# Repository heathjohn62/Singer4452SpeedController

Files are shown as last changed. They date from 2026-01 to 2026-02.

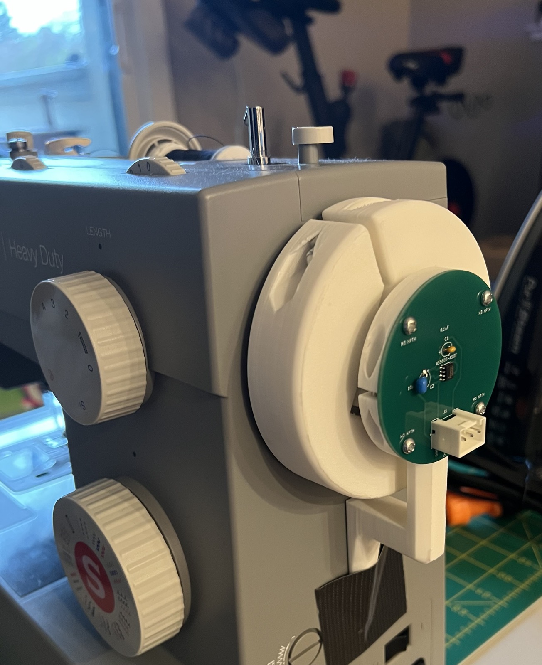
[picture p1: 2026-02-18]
images/rotary-encoder.jpg

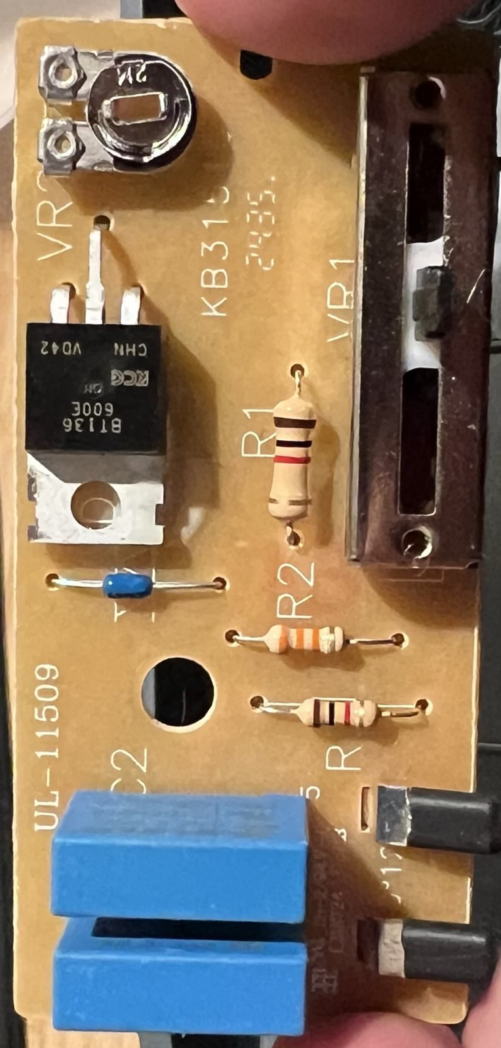
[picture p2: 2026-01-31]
foot-pedal-PCB/original-PCB-images/front.jpg

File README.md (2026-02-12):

# Singer4452-speed-controller

This project implements PID feedback to improve control over the Singer 4452 sewing machine. The modifications are non-destructive to the sewing machine. 

Implement this at your own risk. I do not have an electrical engineering degree nor am I a certified electrician. 120V AC flows through the sewing machine pedal and the PID regulator board, which can electrocute you, start fires, and break things. Don't perform work on circuits that are plugged into the wall. 

As an outline:
1. A rotary encoder tracks the position of the sewing needle by mounting externally to the knob on the side of the machine. The FreeCAD design for the rotary encoder is contained in "rotary-encoder-CAD". Some hardware, a magnet, rubber tape, duct tape, and a ball bearing are also required to assemble this. The PCB for the rotary encoder IC in contained in "speed-sensor-PCB."
2. A network of optoisolated resistors emulate the potentiometer in the existing pedal. Resistance is programmed by a MCU. The MCU and resistor network are enclosed in a chasis, and the design for the PCB is in the folder "Regulator-PCB." The STM32 was programmed in the STM32CubeIDE using the files in the folder "sewing-PID-STM32-program".
3. The circuit board in the original pedal is redesigned. The slide potentiometer provides input to the MCU instead of providing the timing to an RC oscillator as in the original pedal. The RC osillator is timed by the variable resistor network in the regulator PCB. The BT136-600E triac is exchanged for a higher current BT137-600E, and an additional 100 ohm and 0.1uF snubber is added to mitigate stress on the motor and triac. A fuse and varistor are added as short circuit and overvoltage protection. 

Errors and other notes:
- In my original rotary encoder design, pin 5 on the AS5600-ASOT was grounded. This was a mistake, and the pin should be left open. This is now fixed in KiCAD, but for my own sewing machine I just pried the IC pin off of the PCB. 
- The 5V barrel jack runs directly into the enclosure when positioned as it currently is on the PCB. I cut the barrel off and soldered the wires directly to the PCB. This is not currently fixed in the KiCAD design. 
- The AC mains connect to the foot pedal using 0.110" quick-connect tabs. I designed the board for two-prong 0.187" tabs (TE 1-726388-2), which don't fit the mains cables. I didn't want to pay for shipping again, so I bent one of the two prongs on the tabs so that one could be soldered into the PCB and the other into the mains cable. This is fine, but the better part to use would be something like TE 62395-1. 
- "foot-pedal-PCB" contains a folder "spice" with a (very approximate) simulation of the triac trigger circuit in the foot pedal. I used this to better understand the circuit in the original pedal and improve the design. In my hands, the triac model used by the simulation refuses to latch on PC, but works great on mac. 
- **This is likely not the best solution to this problem**. Using an optoisolated resistor network to adjust an RC timer takes up a ton of space and parts, and could be replaced by a circuit that exactly controls the phase angle modulation using only few optoisolators. I did not know I would be redesigning the foot pedal PCB after designing the regulator PCB. I'm now satisfied with the handling of my Singer 4452, so I have no plans to engineer this further. 
- Materials I ordered for this project can be found in the "orders" folder. Other things you would need include a soldering iron, hot air rework station or reflow oven, a drill, wire crimpers, STLink/V2 debugger and TAG-connect adapter, some metric machine screws and standoffs. I recommend anti-static precautions when working with STM32s.

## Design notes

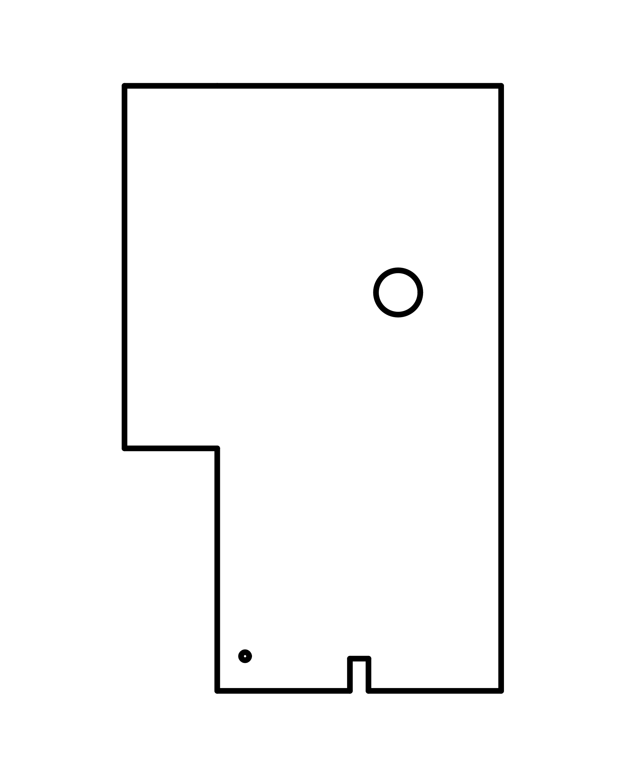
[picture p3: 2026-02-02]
foot-pedal-PCB/board-outline-CAD/board_outline-Page.png

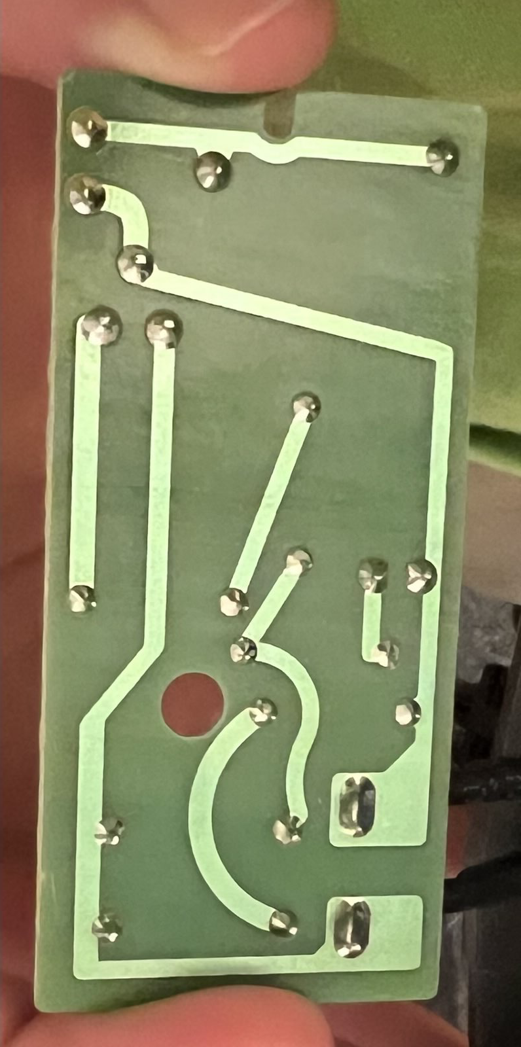
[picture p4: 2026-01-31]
foot-pedal-PCB/original-PCB-images/back.jpg

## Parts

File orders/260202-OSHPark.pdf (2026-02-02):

Invoice for | , generated 2026-02-02

Name
Email
Order ID

PCB : 260202-gerbers
Set Cost | $60.80 USD per set of 3
PCB Quantity | 3 (1 set of 3)
Project Subtotal | $60.80 USD

Shipping Information
Shipping Method | USPS Free Shipping
Shipping Cost | $0.00 USD
Shipping Address

Billing Information
Order date
Payment date
Payment method | Paypal
Payment status | Paid
Shipping Cost | $0.00 USD
Order Items | $60.80 USD
Total cost | $60.80 USD

OSH Park
311 B Ave
Suite B
Lake Oswego, OR 97034

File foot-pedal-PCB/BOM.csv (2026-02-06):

Reference | Qty | OrderQnty | Value | MFG | Mouser # | Description
C1,C2,C3 | 3 | 10 | 0.1uF | Vishay | 594-222233627104 | Safety Capacitors .1uF 10% 275volts
D1 | 1 | 2 | DB3 |  | 511-DB3 | 32V 2A Bidirectional trigger diode, DO-35
J1,J2 | 2 | 10 | 1-726388-2 | TE Connectivity | 571-1-726388-2 | Tab terminal,PCB, FASTON 187, straight TE Connectivity FASTON .187 Series , Straight Mount Angle PCB Tab Terminal, 4.75 x 0.81mm Tin Plated
Q1 | 1 | 2 | BT137-600E |  | 771-BT137-600E | Triacs RAIL TRIAC
R1 | 1 | 2 | 1k | Vishay | 71-CPF31K0000FKE14 | Metal Film Resistors - Through Hole 3watts 1Kohms 1% 100ppm
R2 | 1 | 2 | 22k | Vishay | 594-SFR25H0002202FA5 | Metal Film Resistors - Through Hole SFR25H 1% A5 22K
R3 | 1 | 2 | 1k |  | 594-SFR25H0001001FA5 | Metal Film Resistors SFR25H 1% A5 1K0
R4 | 1 | 2 | 100 | Vishay | 71-CPF3100R00FKE14 | Metal Film Resistors 3watts 100ohms 1% 100ppm
R5 | 1 | 2 | 200k | Vishay | 594-PR01000102003FA5 | Metal Film Resistors PR01 1% A5 200K
RV1 | 1 | 2 | 100k | Alpha (Taiwan) | 312-219BF-100K | Trimmer Resistors - Through Hole T7 YA 100K 20% BO e2
RV2 | 1 | 2 | 20k | Bourns | 652-3329H-1-203LF | Trimmer Resistors - Through Hole 1/4"RND 20KOHMS 10% 0.5WATTS

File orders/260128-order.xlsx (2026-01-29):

MFG # | Digikey # | Description | Qnty | MFG | Supplier | Notes | Link
SVH-21T-1.1 | 455-SVH-21T-1.1CT-ND | CONN SOCKET 18-22AWG CRIMP TIN | 30 | JST Sales America Inc. | Digikey | Solder wires directly onto the regulator PCB, use these external connectors to connect to pedal and rotary encoder.
B3P-VH-FB-B | 455-B3P-VH-FB-B-ND | CONN HEADER VERT 3POS 3.96MM | 10 | JST Sales America Inc. | Digikey
VHR-3N | 455-1184-ND | CONN RCPT HSG 3POS 3.96MM | 10 | JST Sales America Inc. | Digikey |  | https://www.digikey.com/en/products/detail/jst-sales-america-inc/VHR-3N/608625

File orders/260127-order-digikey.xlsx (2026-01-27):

Manufacturer Part # | Digikey Part # | Description | Qnty | MFG | Supplier | Notes | Link
AS5600-ASOT | AS5600-ASOTCT-ND | IC SENSOR MAG ROTARY 12BIT 8SOIC | 2 | ams-OSRAM USA Inc. | Digikey | Magnet rotary position sensor, 3.3V supply. | https://www.digikey.com/en/products/detail/ams-osram-usa-inc/AS5600-ASOT/4914338
STM32C092KCT6 | 497-STM32C092KCT6-ND | ARM® Cortex®-M0+ STM32C0 Microcontroller IC 32-Bit 48MHz 256KB (256K x 8) FLASH 32-LQFP (7x7) | 2 | STMicroelectronics | Digikey | Basic MCU | https://www.digikey.com/en/products/detail/stmicroelectronics/STM32C092KCT6/25935636
TRE06S050-A-01E03 VI | 2034-TRE06S050-A-01E03VI-ND | 5V 6 W AC/DC External Wall Mount (Class II) Adapter Fixed Blade Input | 1 | Cincon | Digilkey | Power Supply | https://www.digikey.com/en/products/detail/cincon-electronics-co-ltd/TRE06S050-A-01E03-VI/12168086
LP2985IM5X-3.3/NOPB | LP2985IM5X-3.3/NOPBCT-ND | Linear Voltage Regulator IC Positive Fixed 1 Output 150mA SOT-23-5 | 2 | TI | Digikey | LDO Regulator | https://www.digikey.com/en/products/detail/texas-instruments/LP2985IM5X-3-3-NOPB/367679
PJ-059A | CP-059A-ND | CONN PWR JACK 2X5.5MM SOLDER | 2 | Same Sky | Digikey | Power Connector | https://www.digikey.com/en/products/detail/same-sky-formerly-cui-devices/PJ-059A/1644607
LH1546AT | 751-LH1546AT-ND | Solid State Photo-Coupled Relay (Photorelay) SPST-NO (1 Form A) 6-DIP (0.300", 7.62mm) | 17 | Vishay | Digikey | SSR Relay ( I need 12) | https://www.digikey.com/en/products/detail/vishay-semiconductor-opto-division/LH1546AT/4072652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
LR1F680R | A105963CT-ND | 680 Ohms ±1% 0.6W Through Hole Resistor Axial Metal Film | 50 | TE Connectivity | Digikey | For LED current limit in SSR | https://www.digikey.com/en/products/detail/te-connectivity-passive-product/LR1F680R/2381276
2N3904 | 4878-2N3904CT-ND | Bipolar (BJT) Transistor NPN 40 V 200 mA 300MHz 625 mW Through Hole TO-92 | 20 | Diotec Semiconductor | Digikey | To drive LED in SSR (12) | https://www.digikey.com/en/products/detail/diotec-semiconductor/2N3904/13164701
RNF14FTD22R1 | RNF14FTD22R1CT-ND | 22.1 Ohms ±1% 0.25W, 1/4W Through Hole Resistor Axial Flame Retardant Coating, Safety Metal Film | 10 | Stackpole Electronics Inc | Digikey | Resistance Grid | https://www.digikey.com/en/products/detail/stackpole-electronics-inc/RNF14FTD22R1/1706712
MFR-25FRF52-44R2 | 13-MFR-25FRF52-44R2CT-ND | 44.2 Ohms ±1% 0.25W, 1/4W Through Hole Resistor Axial Metal Film | 10 | YAGEO | Digikey | Resistance Grid | https://www.digikey.com/en/products/detail/yageo/MFR-25FRF52-44R2/14761
MFR-25FBF52-88R7 | 88.7XBK-ND | 88.7 Ohms ±1% 0.25W, 1/4W Through Hole Resistor Axial Metal Film | 10 | YAGEO | Digikey | Resistance Grid | https://www.digikey.com/en/products/detail/yageo/MFR-25FBF52-88R7/12785
MFR-25FBF52-178R | 178XBK-ND | 178 Ohms ±1% 0.25W, 1/4W Through Hole Resistor Axial Metal Film | 10 | YAGEO | Digikey | Resistance Grid | https://www.digikey.com/en/products/detail/yageo/MFR-25FBF52-178R/12845
MFR-25FBF52-357R | 357XBK-ND | 357 Ohms ±1% 0.25W, 1/4W Through Hole Resistor Axial Metal Film | 10 | YAGEO | Digikey | Resistance Grid | https://www.digikey.com/en/products/detail/yageo/MFR-25FBF52-357R/12911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
MFR-25FBF52-715R | 715XBK-ND | 715 Ohms ±1% 0.25W, 1/4W Through Hole Resistor Axial Metal Film | 10 | YAGEO | Digikey | Resistance Grid | https://www.digikey.com/en/products/detail/yageo/MFR-25FBF52-715R/12983
MFR-25FBF52-1K43 | 13-MFR-25FBF52-1K43-ND | 1.43 kOhms ±1% 0.25W, 1/4W Through Hole Resistor Axial Metal Film | 10 | YAGEO | Digikey | Resistance Grid | https://www.digikey.com/en/products/detail/yageo/MFR-25FBF52-1K43/13042
MFR-25FBF52-2K87 | 2.87KXBK-ND | 2.87 kOhms ±1% 0.25W, 1/4W Through Hole Resistor Axial Metal Film | 10 | YAGEO | Digikey | Resistance Grid | https://www.digikey.com/en/products/detail/yageo/MFR-25FBF52-2K87/13116
MFR-25FRF52-5K76 | 13-MFR-25FRF52-5K76CT-ND | 5.76 kOhms ±1% 0.25W, 1/4W Through Hole Resistor Axial Metal Film | 10 | YAGEO | Digikey | Resistance Grid | https://www.digikey.com/en/products/detail/yageo/MFR-25FRF52-5K76/14962
MFR-25FBF52-11K5 | 11.5KXBK-ND | 11.5 kOhms ±1% 0.25W, 1/4W Through Hole Resistor Axial Metal Film | 10 | YAGEO | Digikey | Resistance Grid | https://www.digikey.com/en/products/detail/yageo/MFR-25FBF52-11K5/13230
MFR-25FBF52-23K2 | 23.2KXBK-ND | 23.2 kOhms ±1% 0.25W, 1/4W Through Hole Resistor Axial Metal Film | 10 | YAGEO | Digikey | Resistance Grid | https://www.digikey.com/en/products/detail/yageo/MFR-25FBF52-23K2/13288
MFR-25FRF52-46K4 | 13-MFR-25FRF52-46K4CT-ND | 46.4 kOhms ±1% 0.25W, 1/4W Through Hole Resistor Axial Metal Film | 10 | YAGEO | Digikey | Resistance Grid | https://www.digikey.com/en/products/detail/yageo/MFR-25FRF52-46K4/15046
MFR-25FBF52-93K1 | 93.1KXBK-ND | 93.1 kOhms ±1% 0.25W, 1/4W Through Hole Resistor Axial Metal Film | 10 | YAGEO | Digikey | Resistance Grid | https://www.digikey.com/en/products/detail/yageo/MFR-25FBF52-93K1/13467
STS232050UL40 | 283-STS232050UL40CT-ND | 15V Clamp 4A (8/20µs) Ipp Tvs Diode Surface Mount SOT-23 | 10 | Eaton - Electronics Division | Digikey | MCU protection | https://www.digikey.com/en/products/detail/eaton-electronics-division/STS232050UL40/13280445
1.5KE6.8CA | 13-1.5KE6.8CA/BCT-ND | TVS Diode for power supply (Bidirectional) | 2 | YAGEO | Digikey | MCU protection
1.5KE6.8A | 1.5KE6.8ALFCT-ND | TVS Diode for power 5V supply (Unidirectional) | 2 | Littelfuse Inc. | Digikey | MCU protection and reverse polarity protection. | https://www.digikey.com/en/products/detail/littelfuse-inc/1-5KE6-8A/285842
C320C104K5R5TA | 399-4264-ND | 0.1 µF ±10% 50V Ceramic Capacitor X7R Radial | 10 | Kemet | Digikey | Decoupling | https://www.digikey.com/en/products/detail/kemet/C320C104K5R5TA/818040
FG20X7R1H106KRT06 | 445-173297-1-ND | 10 µF ±10% 50V Ceramic Capacitor X7R Radial | 10 | TDK Corporation | Digikey | Power Supply Cap for AS5600 | https://www.digikey.com/en/products/detail/tdk-corporation/FG20X7R1H106KRT06/5811902
FG24X7R1E475KRT00 | 445-FG24X7R1E475KRT00-ND | 4.7 µF ±10% 25V Ceramic Capacitor X7R Radial | 10 | TDK Corporation | Digikey | Decoupling | https://www.digikey.com/en/products/detail/tdk-corporation/FG24X7R1E475KRT00/7326742
8019 | 469-1003-ND | Magnet Neodymium Iron Boron (NdFeB) N35 0.250" Dia x 0.250" H (6.35mm x 6.35mm) | 2 | Radial Magnets Inc. | Digikey | Strong magnet | https://www.digikey.com/en/products/detail/radial-magnets-inc/8019/555327
PDB181-K420K-203B | PDB181-K420K-203B-ND | 20k Ohm 1 Gang Linear Panel Mount Potentiometer 1.0 Turns Carbon 0.2W, 1/5W PC Pins | 3 | Bourns | Digikey | for foot pedal | https://www.digikey.com/en/products/detail/bourns-inc/PDB181-K420K-203B/2564752?gclsrc=aw.ds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
B32621A6103J189 | 495-B32621A6103J189CT-ND | 10000 pF Film Capacitor 400V 630V Polypropylene (PP), Metallized - Stacked Radial | 2 | EPCOS - TDK Electronics | Digikey | noise regulation power supply | https://www.digikey.com/en/products/detail/epcos-tdk-electronics/B32621A6103J189/3491369
MFR-25FRF52-10K | 13-MFR-25FRF52-10KCT-ND | 10 kOhms ±1% 0.25W, 1/4W Through Hole Resistor Axial Metal Film | 50 | YAGEO | Digikey | 2N904 Gate Resistor | https://www.digikey.com/en/products/detail/yageo/MFR-25FRF52-10K/14626

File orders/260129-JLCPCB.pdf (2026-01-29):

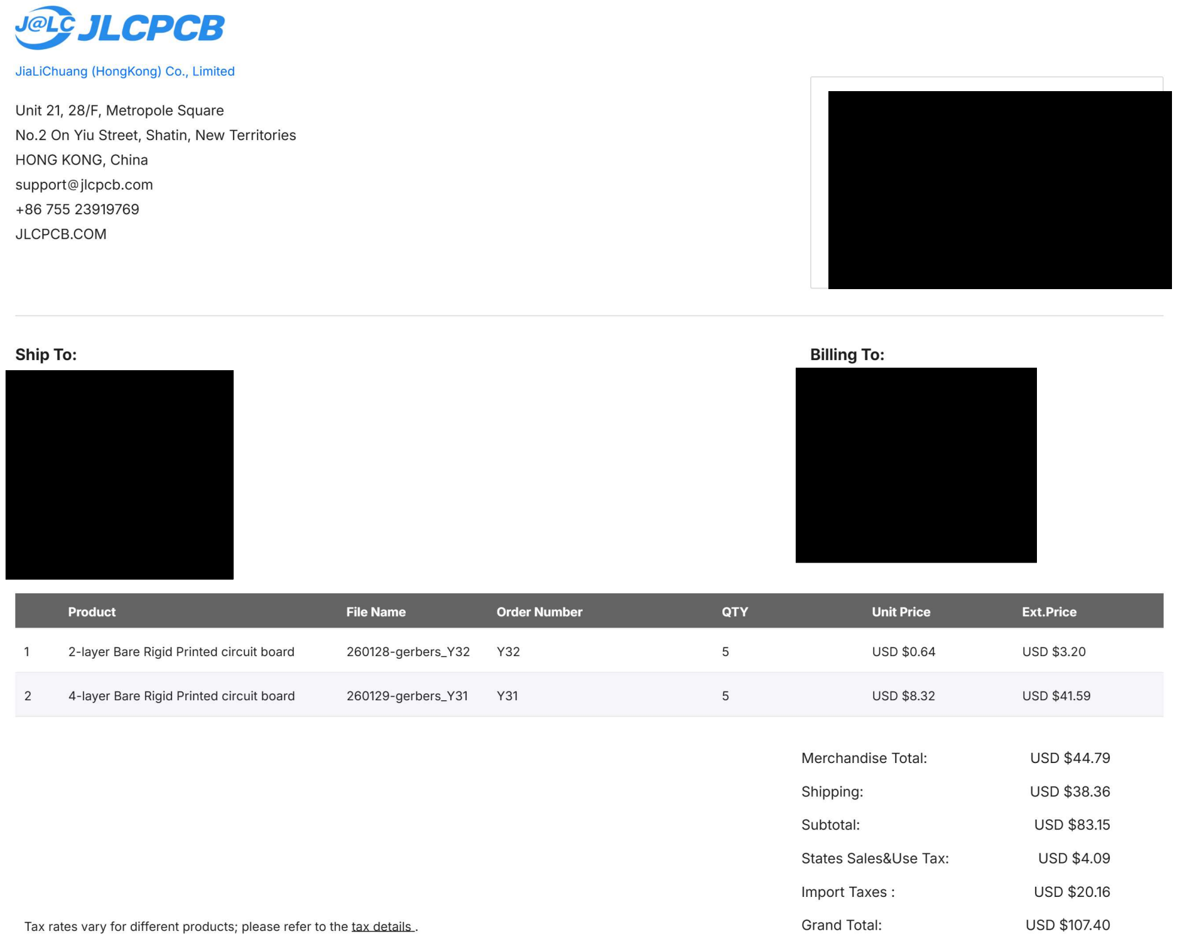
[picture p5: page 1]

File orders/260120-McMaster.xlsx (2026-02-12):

MFG # | Description | Price | Qnty | MFG | Notes | Link
5652N161 | Fabric-Reinforced Multipurpose Neoprene Strip with Adhesive-Back, High-Strength, 2" x 36", 1/16" Thick |  | 1 | Mcmaster Carr |  | https://www.mcmaster.com/5652N161/

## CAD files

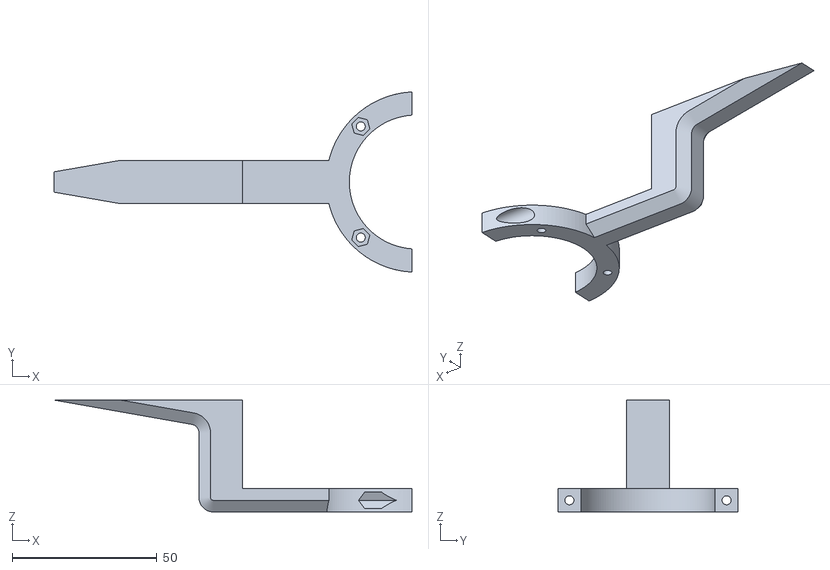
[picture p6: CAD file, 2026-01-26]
rotary-encoder-CAD/260126-lower-PCB-mount.stl
123.5 x 62.1 x 38.6

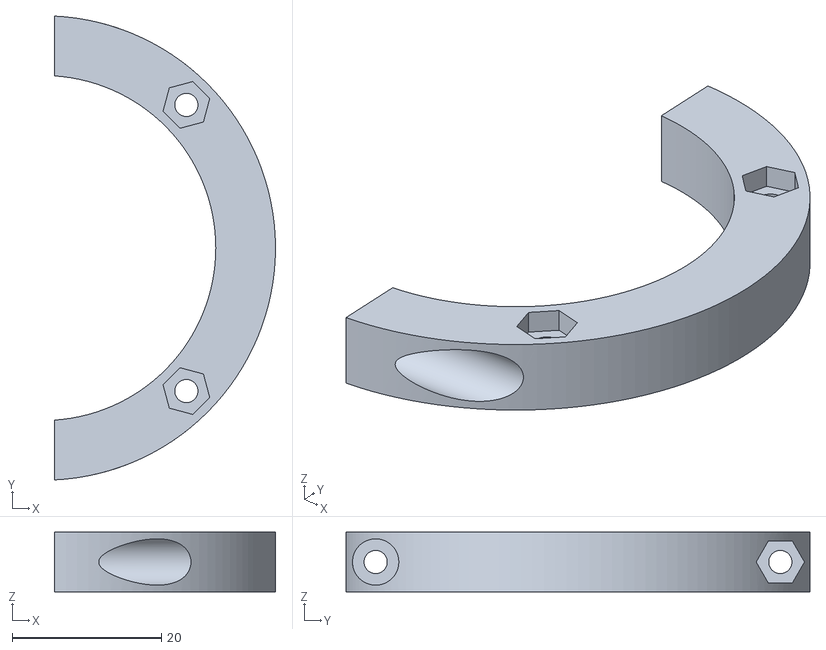
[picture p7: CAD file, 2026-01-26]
rotary-encoder-CAD/260126-upper-PCB-mount.stl
29.6 x 62.1 x 8.00

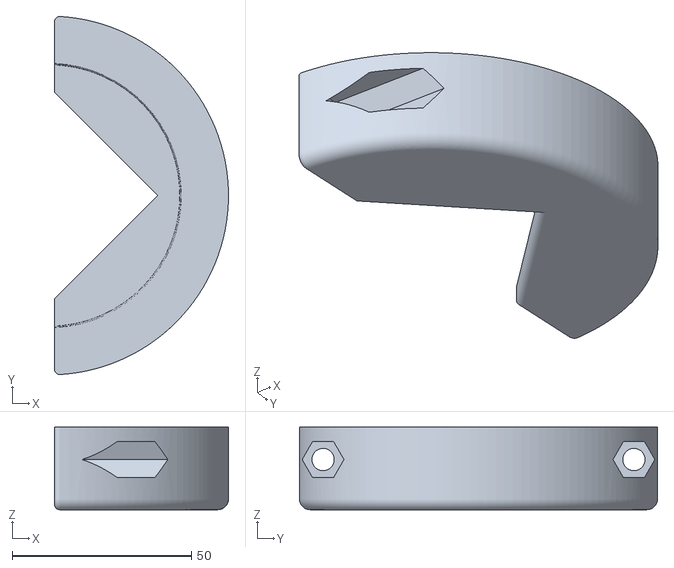
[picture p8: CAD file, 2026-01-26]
rotary-encoder-CAD/260125-upper-grip.stl
48.5 x 99.8 x 23.0

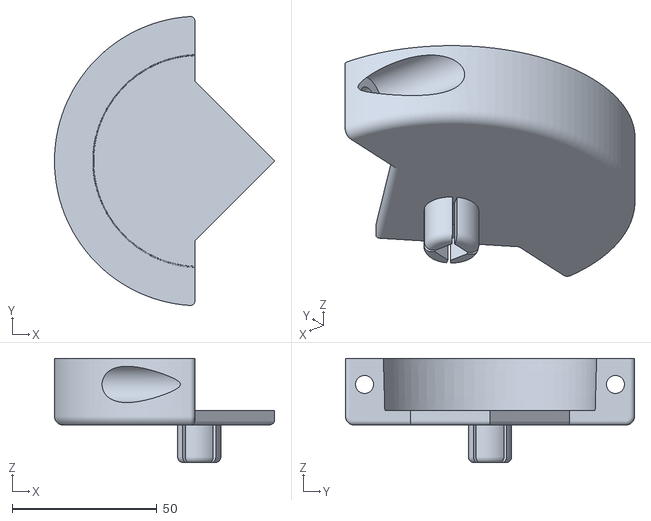
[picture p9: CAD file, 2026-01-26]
rotary-encoder-CAD/260125-lower-grip.stl
76.0 x 99.8 x 36.0

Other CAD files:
foot-pedal-PCB/board-outline-CAD/board_outline.FCStd

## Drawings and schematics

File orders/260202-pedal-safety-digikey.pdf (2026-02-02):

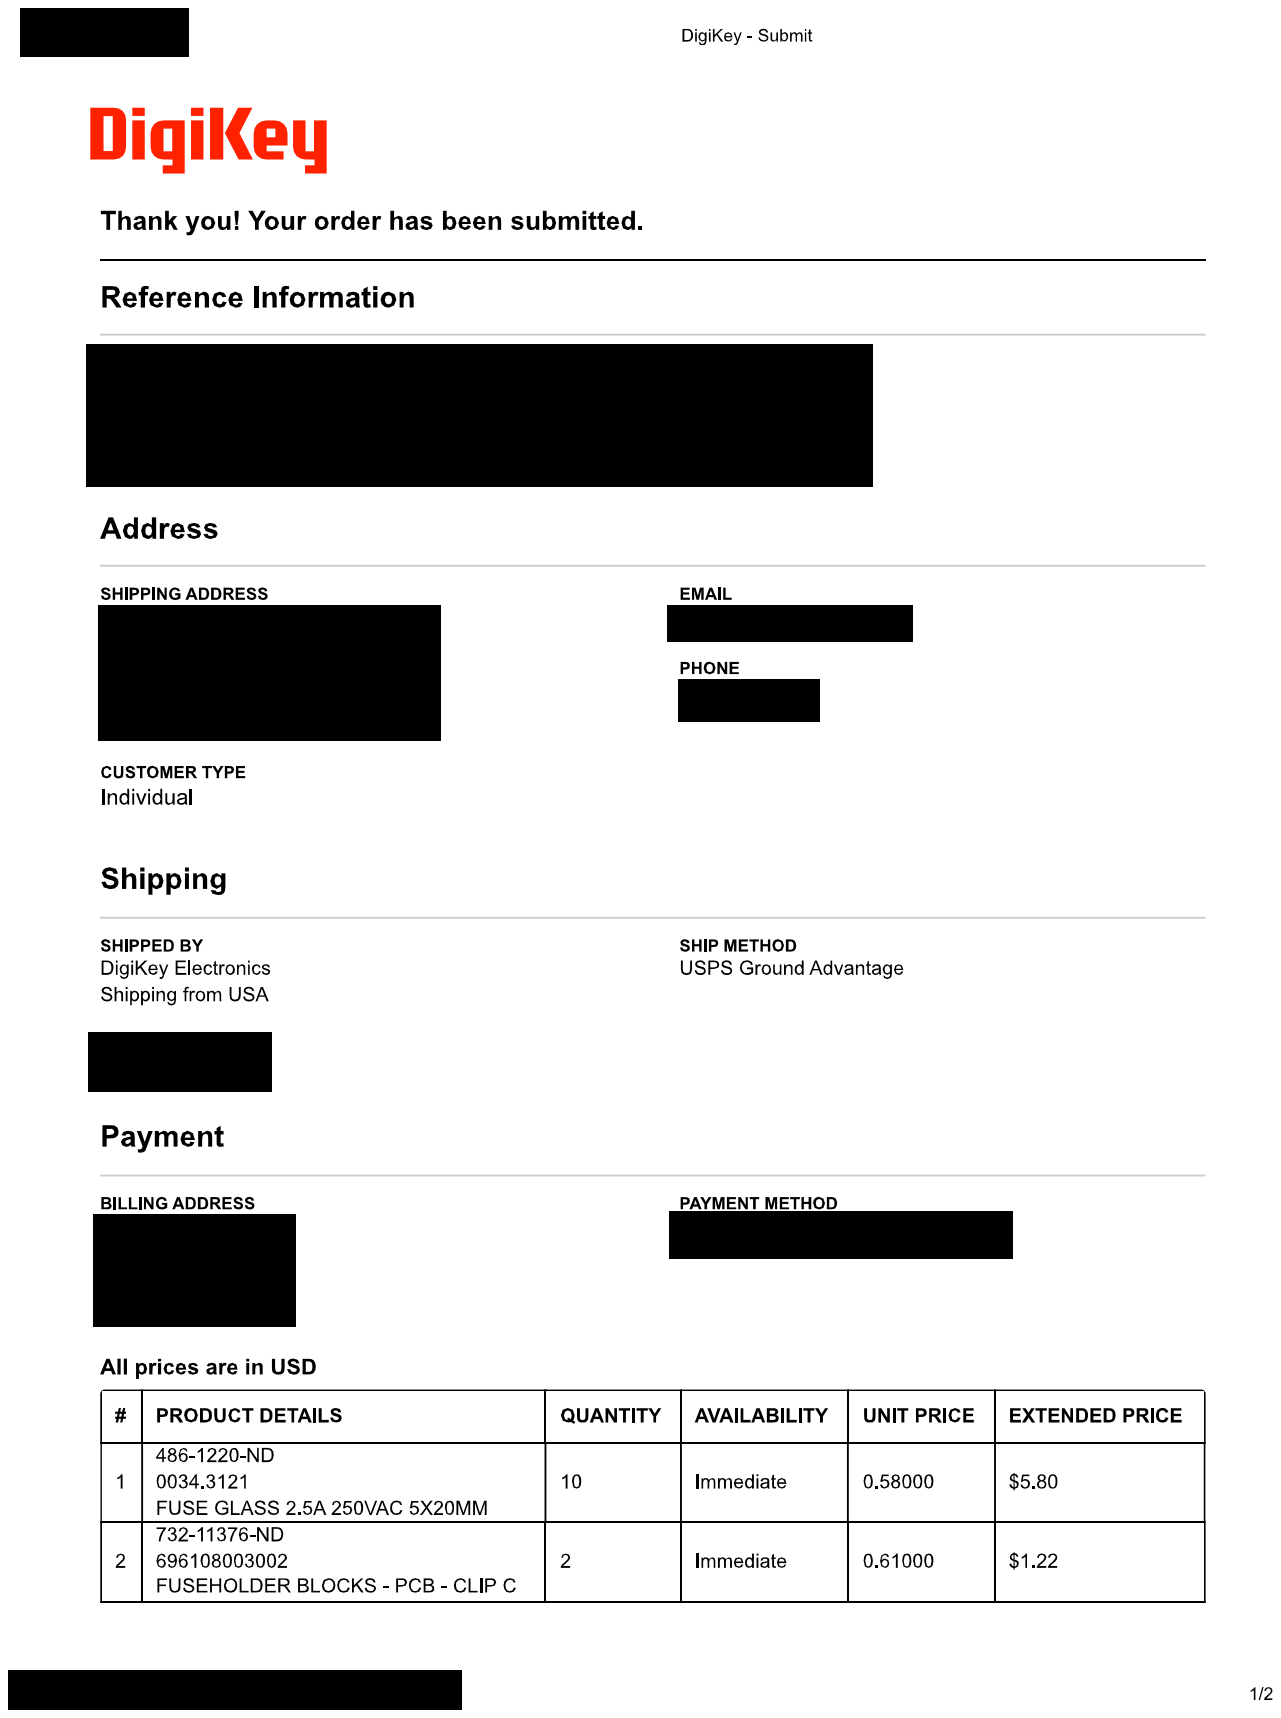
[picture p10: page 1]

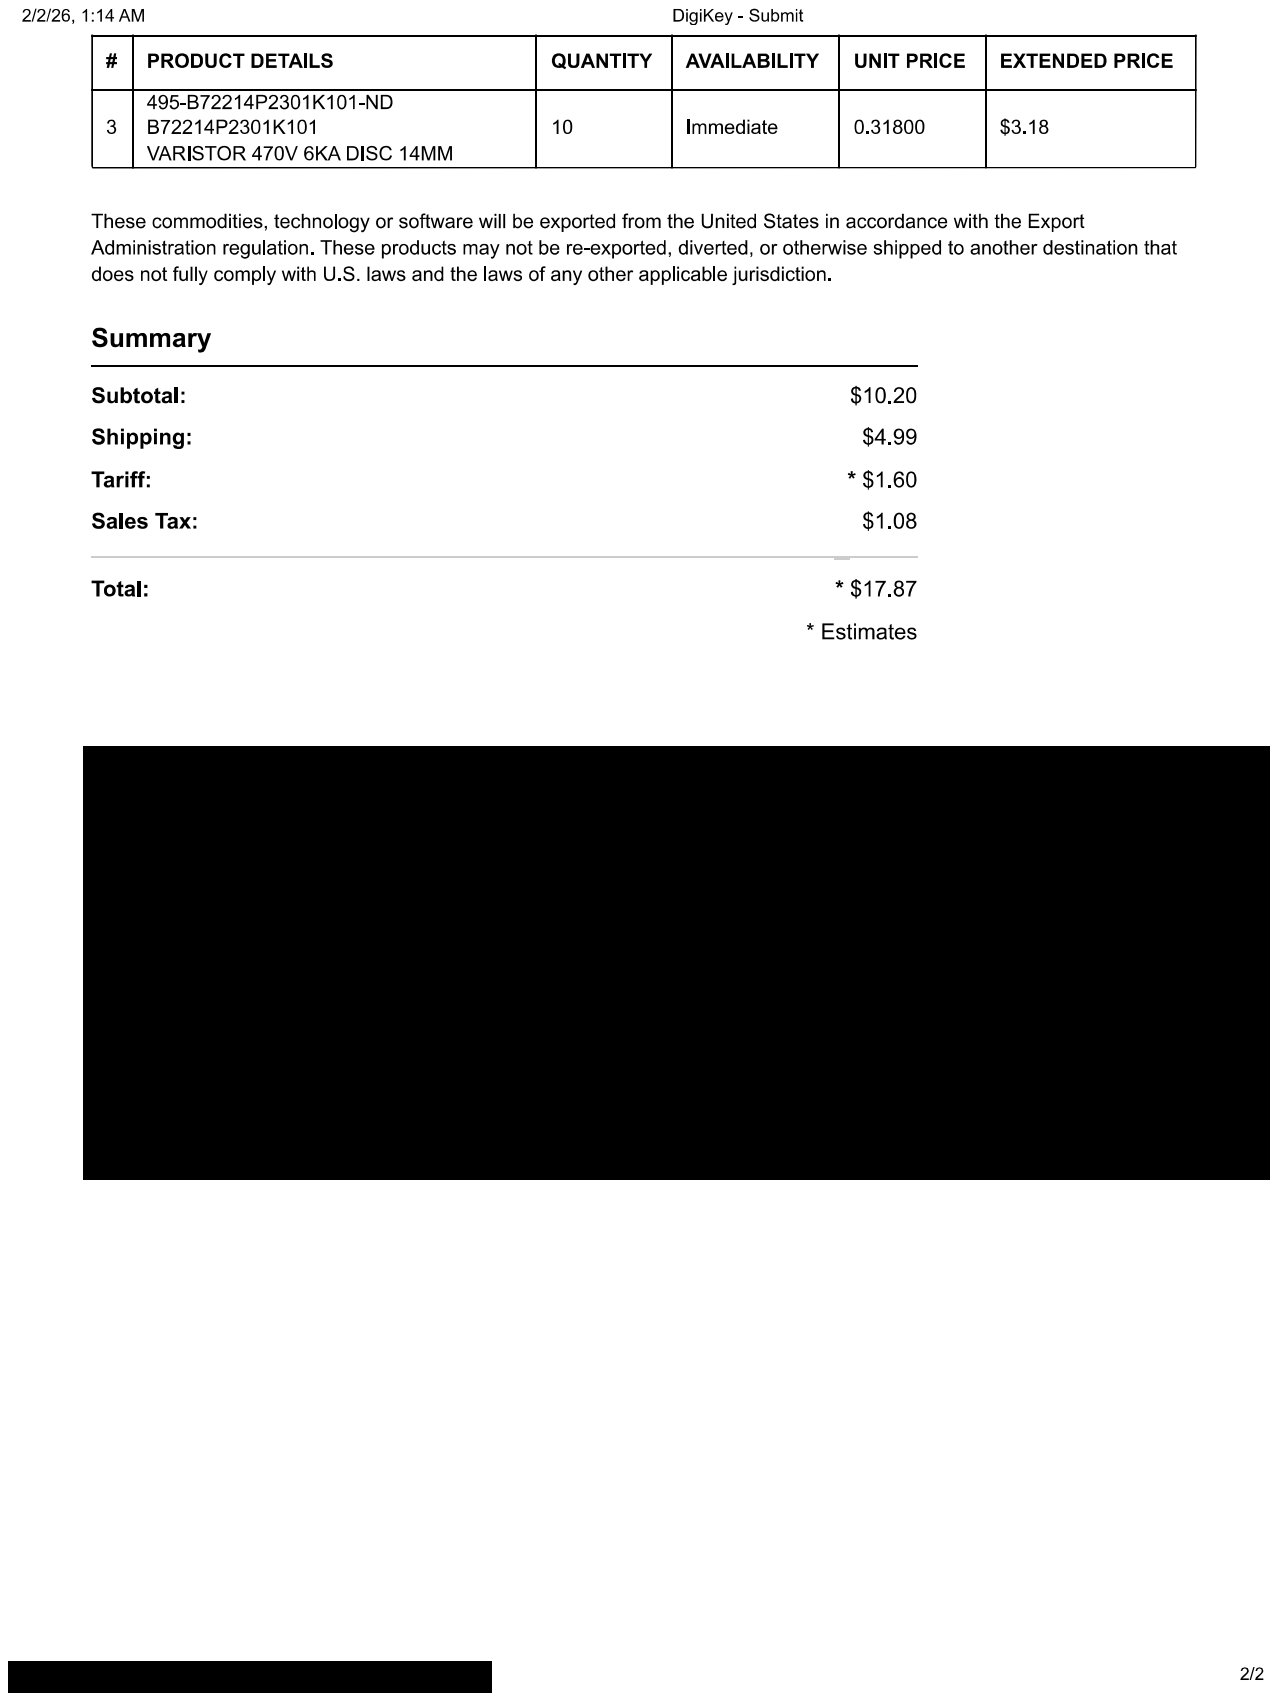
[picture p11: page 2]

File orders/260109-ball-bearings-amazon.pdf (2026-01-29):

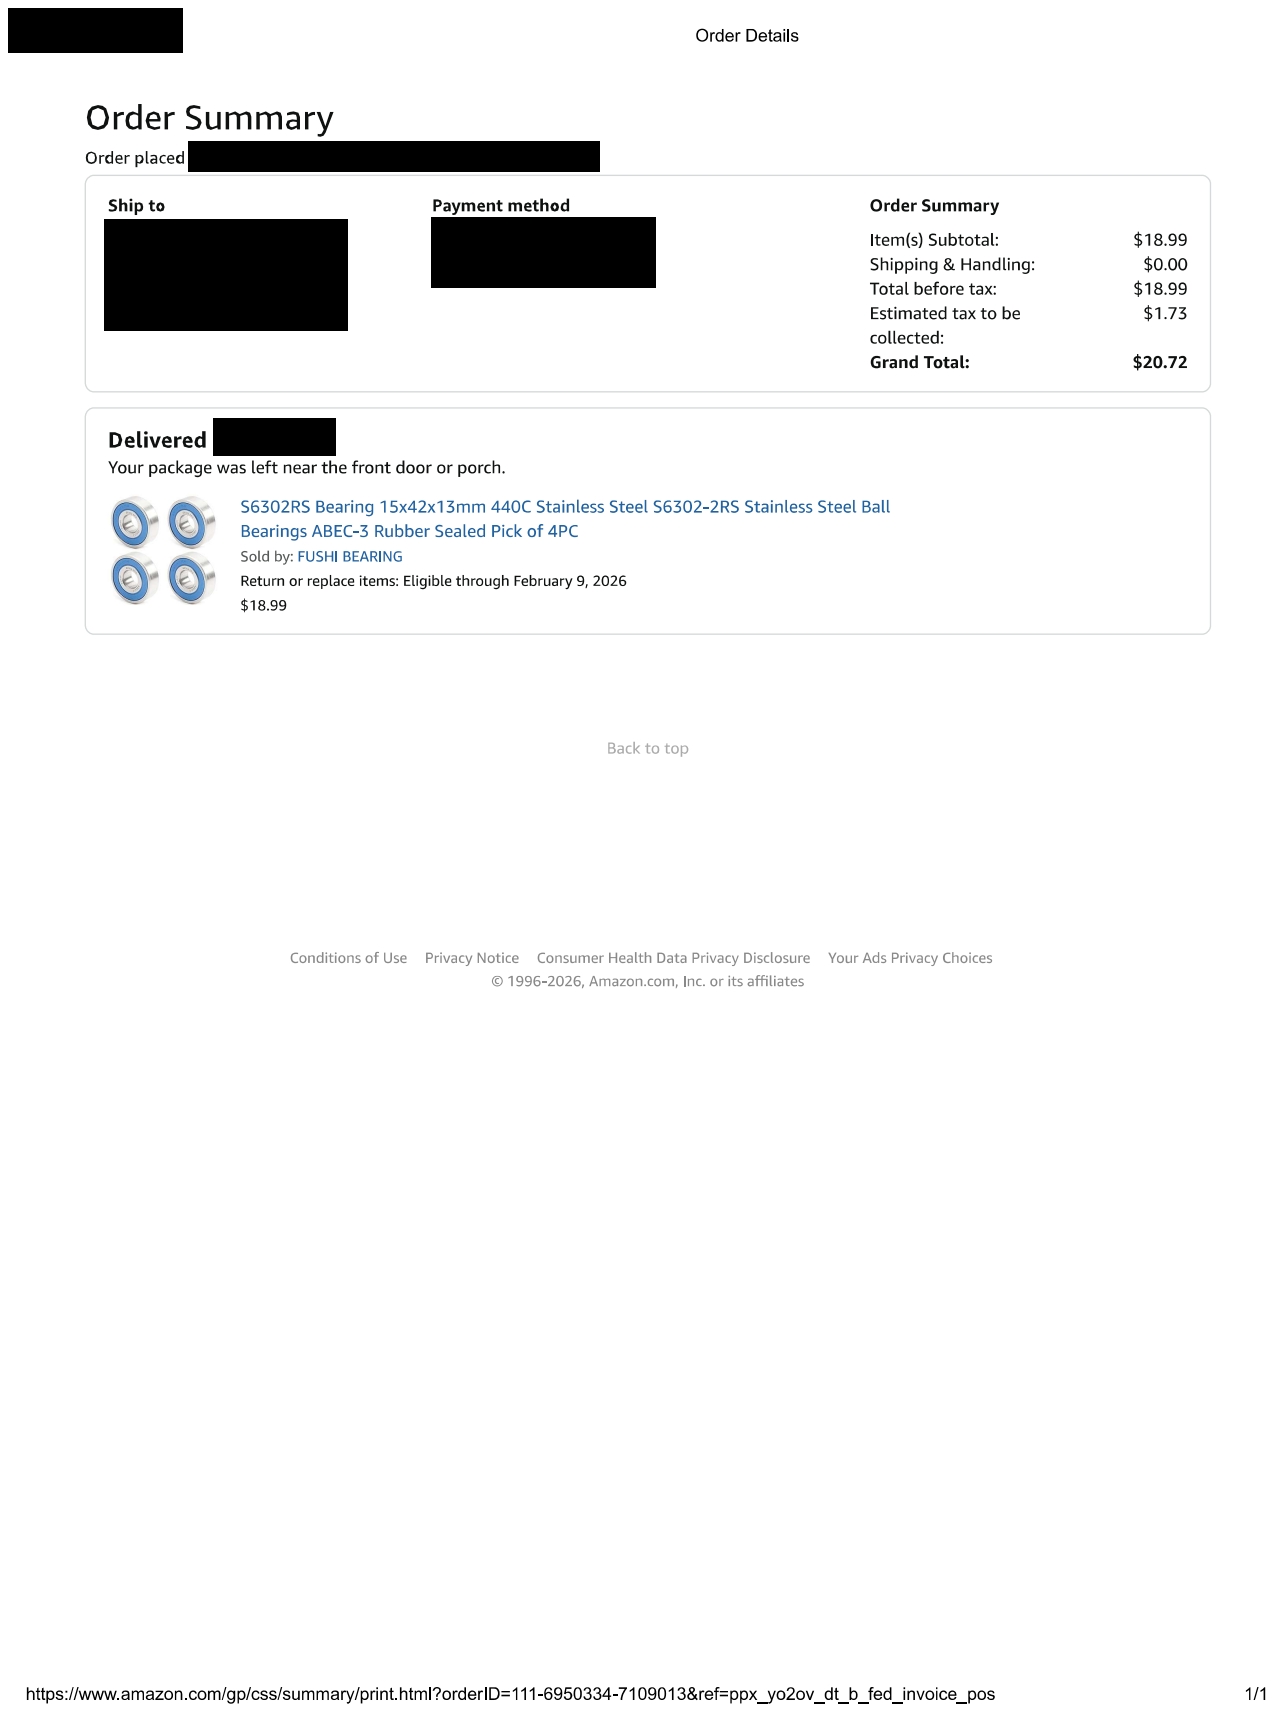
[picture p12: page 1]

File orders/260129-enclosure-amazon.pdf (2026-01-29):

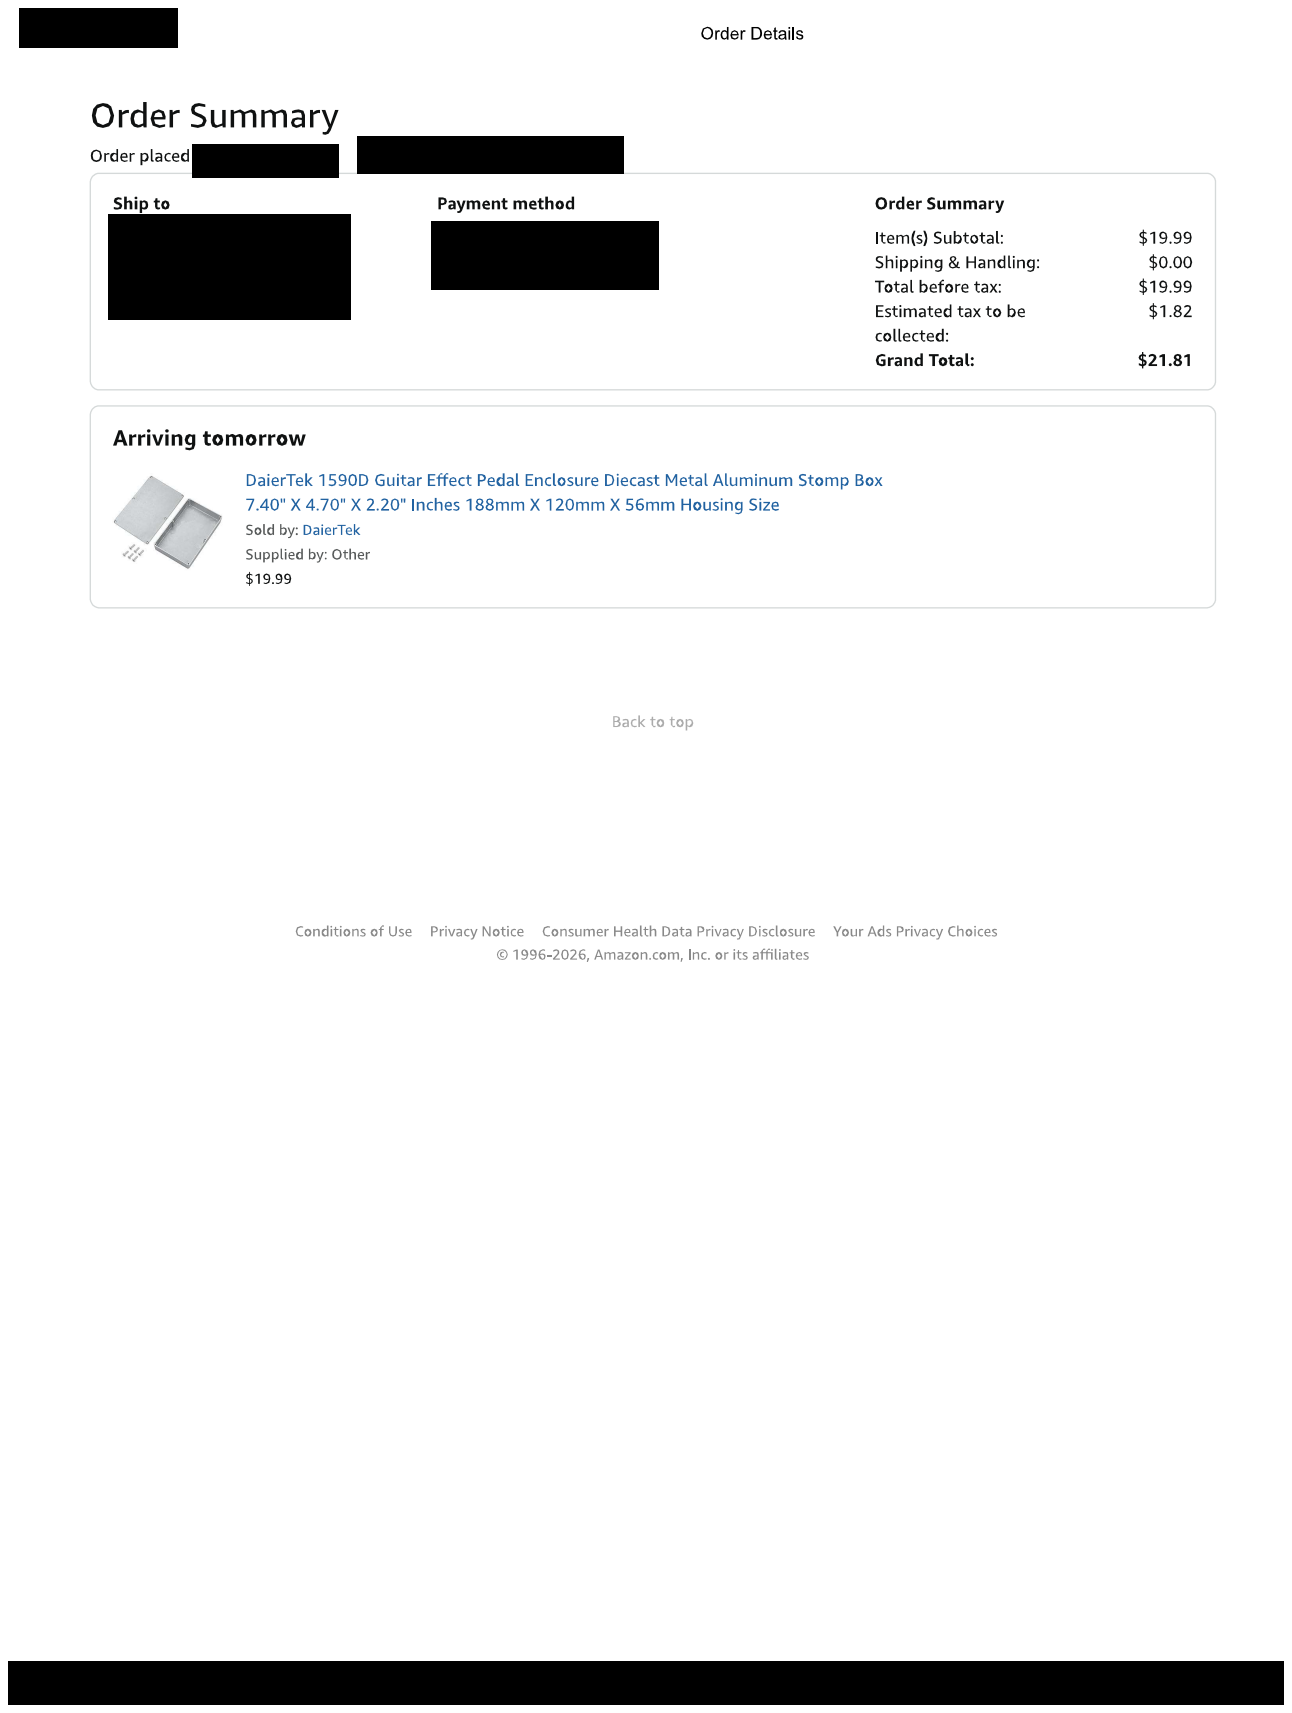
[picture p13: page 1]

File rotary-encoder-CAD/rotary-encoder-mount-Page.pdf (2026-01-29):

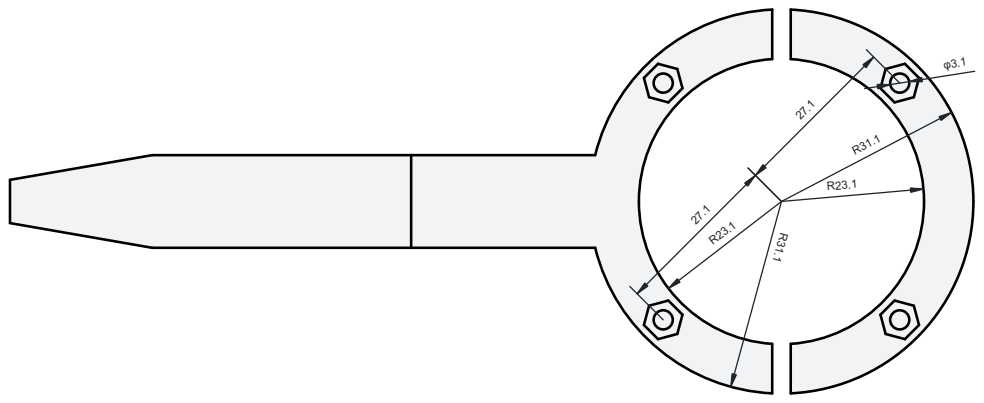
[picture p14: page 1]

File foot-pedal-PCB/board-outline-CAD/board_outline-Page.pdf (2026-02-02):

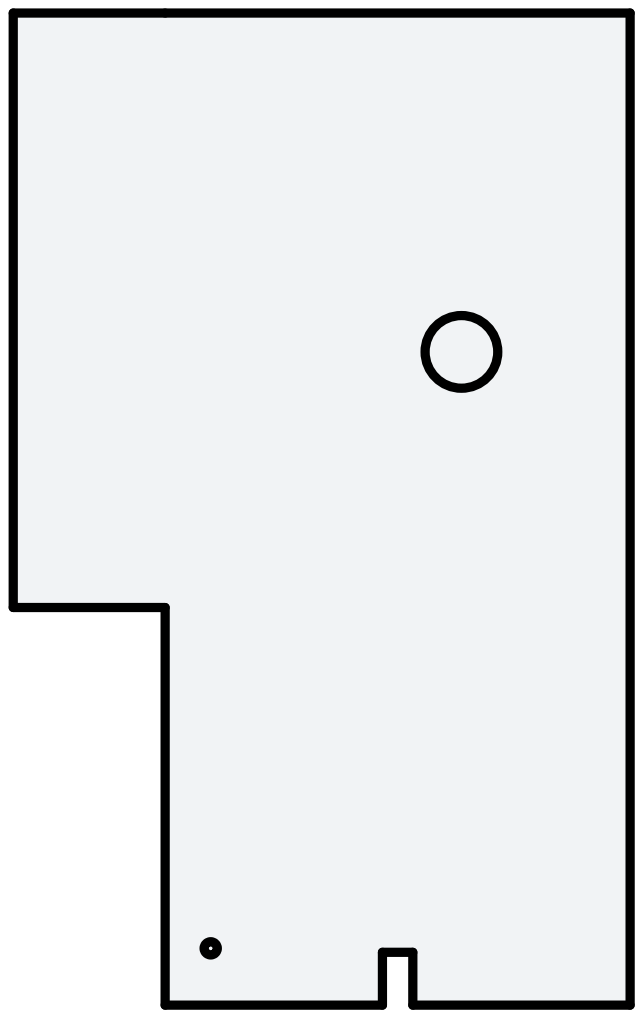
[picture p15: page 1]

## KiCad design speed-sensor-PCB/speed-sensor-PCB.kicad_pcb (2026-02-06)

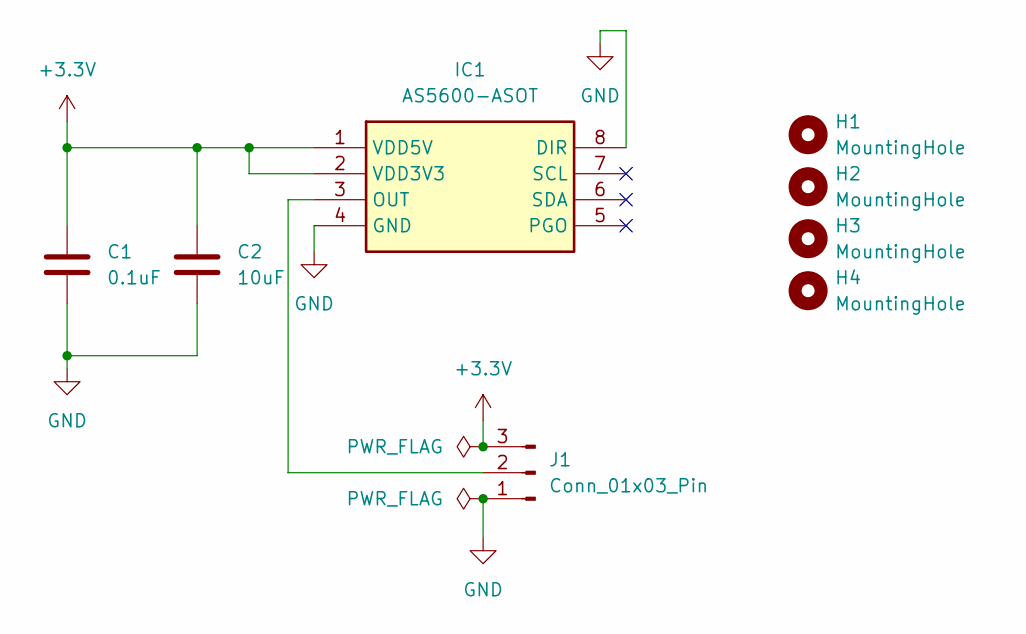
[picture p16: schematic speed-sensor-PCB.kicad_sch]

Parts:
C1: 0.1uF; CAP_C320_KEM; Part # C320C104K5R5TA
C2: 10uF; CP_Radial_Tantal_D5.5mm_P5.00mm; Part # FG20X7R1H106KRT06
H1, H2, H3, H4: MountingHole; MountingHole_3.2mm_M3_ISO7380
IC1: AS5600-ASOT; SOIC-8_3.9x4.9mm_P1.27mm; Mouser Part Number 985-AS5600-ASOT
J1: Conn_01x03_Pin; JST_VH_B3P-VH-FB-B_1x03_P3.96mm_Vertical

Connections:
+3.3V: C1.1, C2.1, IC1.1 (VDD5V), IC1.2 (VDD3V3), J1.3
GND: C1.2, C2.2, IC1.4 (GND), IC1.8 (DIR), J1.1
unnamed: IC1.3 (OUT), J1.2

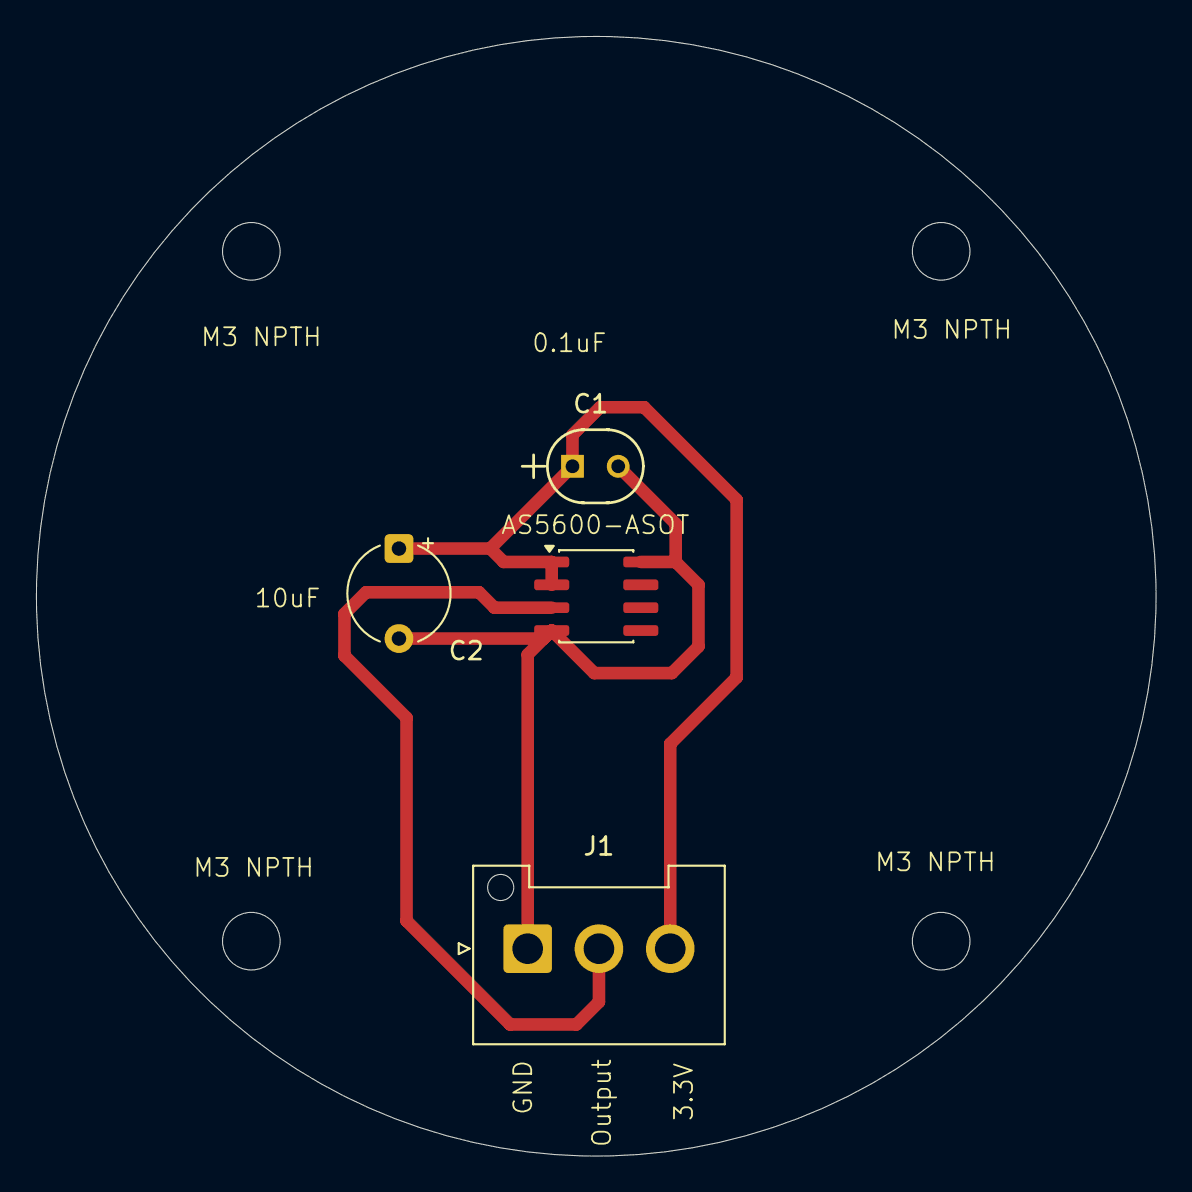
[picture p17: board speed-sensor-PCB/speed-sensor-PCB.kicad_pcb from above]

Board: 2 copper layers, 62.2 x 62.2 mm, 8 parts (0 on the bottom side), 3 nets.

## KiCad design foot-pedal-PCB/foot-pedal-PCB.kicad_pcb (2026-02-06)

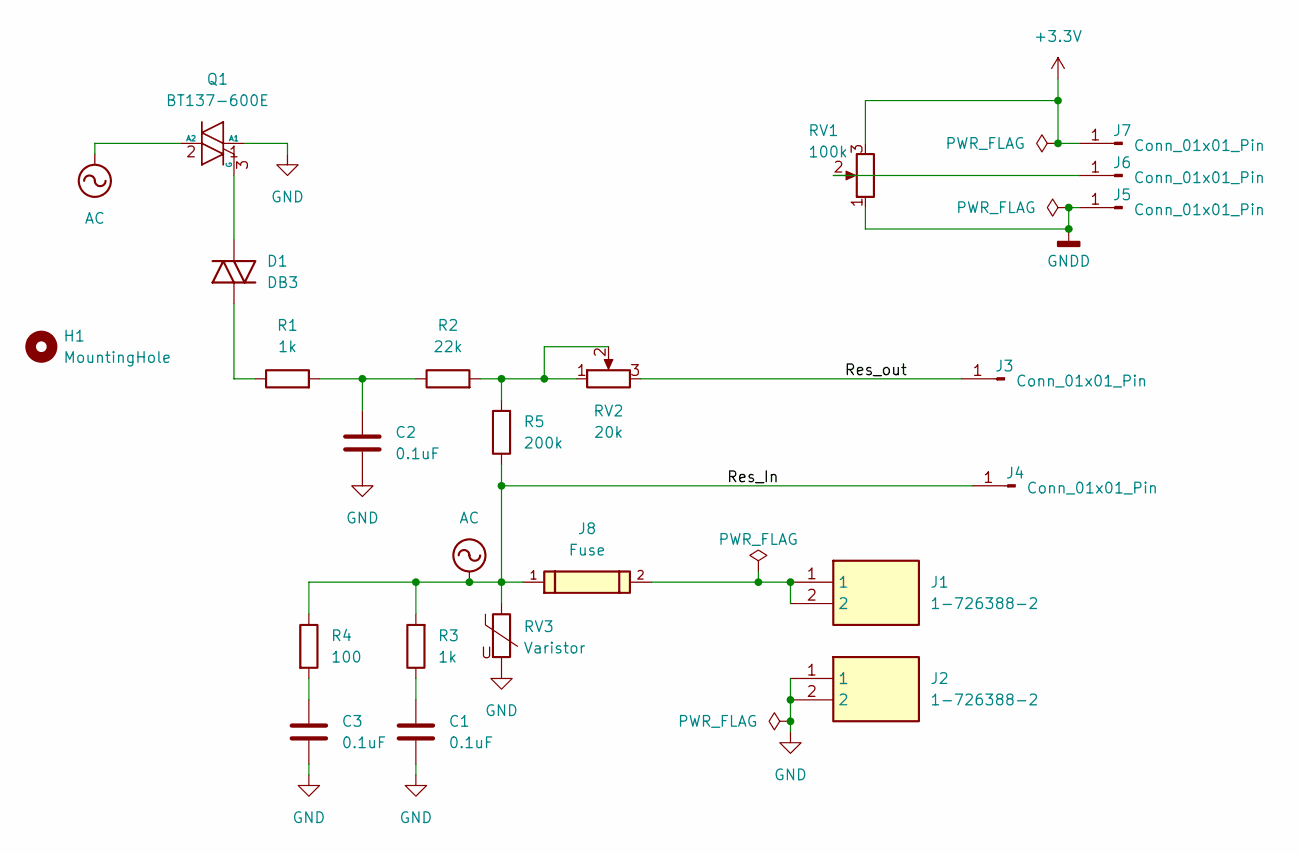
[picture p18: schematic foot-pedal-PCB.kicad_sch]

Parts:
C1, C2, C3: 0.1uF; C_Rect_L18.0mm_W5.0mm_P15.00mm_FKS3_FKP3; MFG # BFC233627104; Mouser # 594-222233627104
D1: DB3; D_DO-35_SOD27_P7.62mm_Horizontal; MFG # DB3; Mouser # 511-DB3
H1: MountingHole; MountingHole_5.5mm
J1, J2: 1-726388-2; 17263882; Mouser # 571-1-726388-2
J3, J4, J5, J6, J7: Conn_01x01_Pin; SolderWire-0.5sqmm_1x01_D0.9mm_OD2.1mm
J8: Fuse; 696108003002; MFG # 696108003002
Q1: BT137-600E; MFG # BT137-600E,127; Mouser # 771-BT137-600E
R1: 1k; R_Axial_DIN0516_L15.5mm_D5.0mm_P20.32mm_Horizontal; MFG # CPF31K0000FKE14; Mouser # 71-CPF31K0000FKE14
R2: 22k; R_Axial_DIN0207_L6.3mm_D2.5mm_P10.16mm_Horizontal; MFG # SFR25H0002202FA500; Mouser # 594-SFR25H0002202FA5
R3: 1k; R_Axial_DIN0207_L6.3mm_D2.5mm_P10.16mm_Horizontal; MFG # SFR25H0001001FA500; Mouser # 594-SFR25H0001001FA5
R4: 100; R_Axial_DIN0516_L15.5mm_D5.0mm_P20.32mm_Horizontal; MFG # CPF3100R00FKE14; Mouser # 71-CPF3100R00FKE14
R5: 200k; R_Axial_DIN0207_L6.3mm_D2.5mm_P10.16mm_Horizontal; MFG # PR01000102003FA500; Mouser # 594-PR01000102003FA5
RV1: 100k; RA2043F2010EB1B100K; MFG # RA2043F-20-10EB1-B100K; Mouser # 312-219BF-100K
RV2: 20k; POT_3329H; MFG # 3329H-1-203LF; Mouser # 652-3329H-1-203LF
RV3: Varistor; VAR_B72214P2301K101; MFG # B72214P2301K101

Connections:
+3.3V: J7.1, RV1.3
/Res_out: J3.1, RV2.3
AC: J4.1, J8.1, Q1.2 (A2), R3.2, R4.1, R5.1, RV3.1
GND: C1.1, C2.1, C3.1, J2.1, J2.2, Q1.1 (A1), RV3.2
GNDD: J5.1, RV1.1
unnamed: C1.2, R3.1
unnamed: C2.2, R1.2, R2.1
unnamed: C3.2, R4.2
unnamed: D1.2 (A), Q1.3 (G)
unnamed: D1.1 (K), R1.1
unnamed: J1.1, J1.2, J8.2
unnamed: J6.1, RV1.2
unnamed: R2.2, R5.2, RV2.1, RV2.2

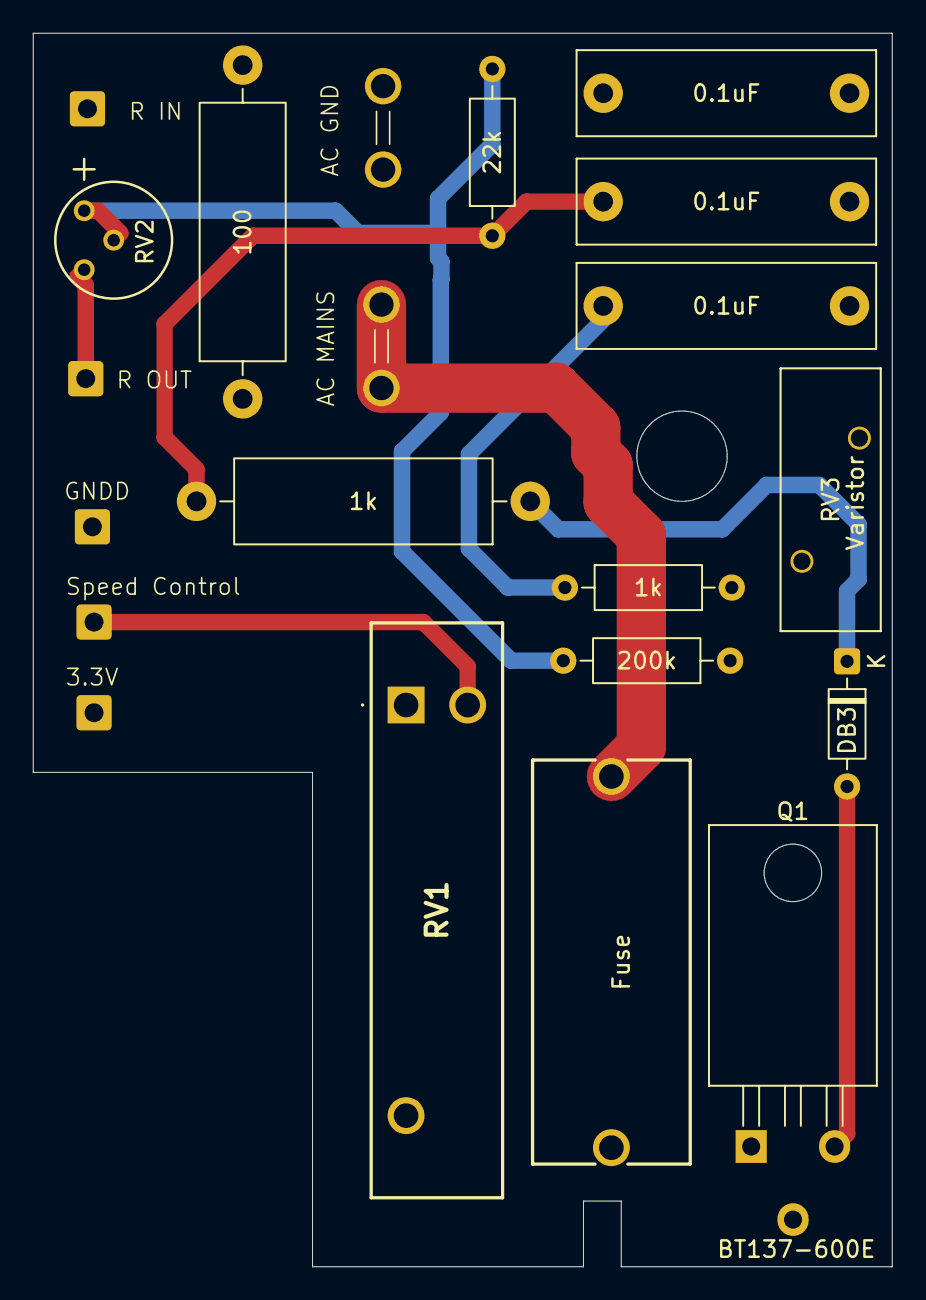
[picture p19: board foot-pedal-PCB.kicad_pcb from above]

Board: 4 copper layers, 52.3 x 75.1 mm, 22 parts (0 on the bottom side), 13 nets.

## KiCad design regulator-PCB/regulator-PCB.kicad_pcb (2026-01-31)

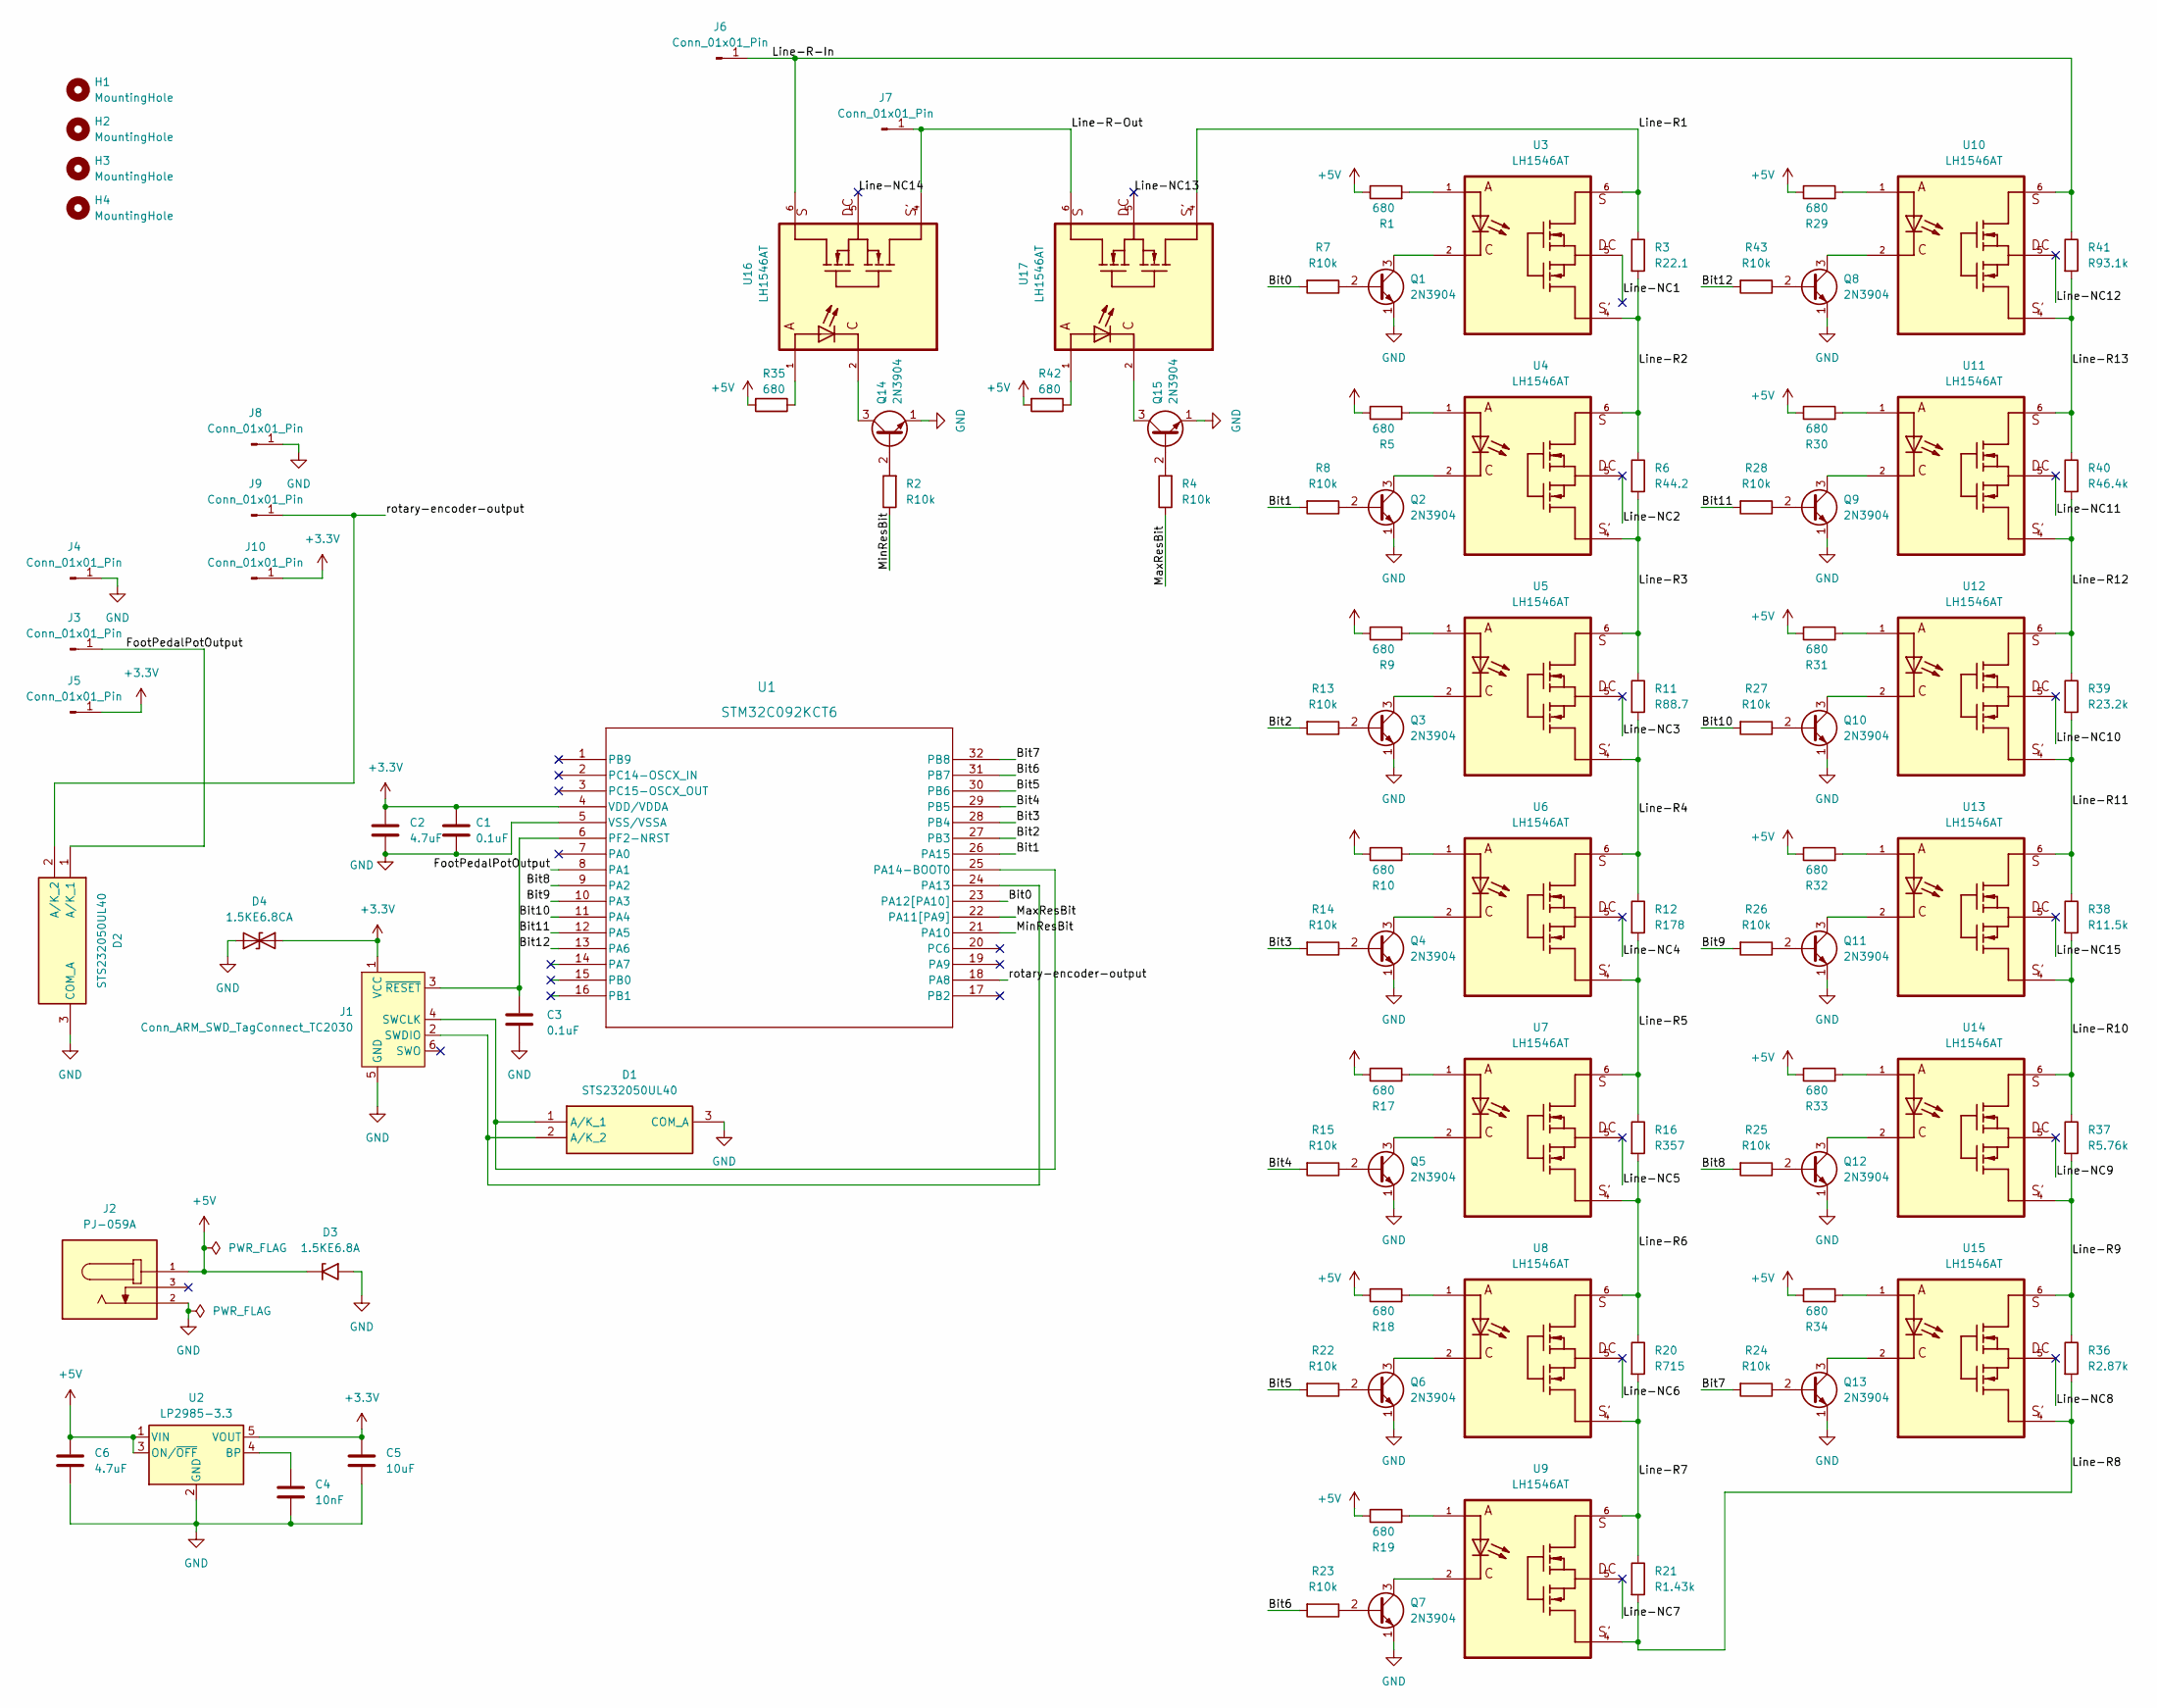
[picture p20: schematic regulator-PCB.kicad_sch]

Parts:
C1, C3: 0.1uF; CAP_C320_KEM; Part # C320C104K5R5TA
C2, C6: 4.7uF; CAPRB500W50L450T300H550; Part # FG24X7R1E475KRT00
C4: 10nF; C_Rect_L13.0mm_W4.0mm_P10.00mm_FKS3_FKP3_MKS4; Part # B32621A6103J189
C5: 10uF; CP_Radial_Tantal_D5.5mm_P5.00mm; Part # FG20X7R1H106KRT06
D1, D2: STS232050UL40; Mouser Part Number 504-STS232050UL40
D3: 1.5KE6.8A; D_DO-201AE_P15.24mm_Horizontal
D4: 1.5KE6.8CA; D_DO-201AE_P15.24mm_Horizontal
H1, H2, H3, H4: MountingHole; MountingHole_4.5mm
J1: Conn_ARM_SWD_TagConnect_TC2030; Tag-Connect_TC2030-IDC-FP_2x03_P1.27mm_Vertical
J2: PJ-059A; CUI_PJ-059A; PARTREV 1.04
J3, J4, J5, J6, J7, J8, J9, J10: Conn_01x01_Pin; SolderWire-0.75sqmm_1x01_D1.25mm_OD2.3mm_Relief
Q1, Q2, Q3, Q4, Q5, Q6, Q7, Q8, Q9, Q10, Q11, Q12, Q13, Q14, Q15: 2N3904; TO-92_Inline
R1, R5, R9, R10, R17, R18, R19, R29, R30, R31, R32, R33, R34, R35, R42: 680; R_Axial_DIN0207_L6.3mm_D2.5mm_P10.16mm_Horizontal; MFG # LR1F680R
R2, R4, R7, R8, R13, R14, R15, R22, R23, R24, R25, R26, R27, R28, R43: R10k; R_Axial_DIN0207_L6.3mm_D2.5mm_P10.16mm_Horizontal; MFG # MFR-25FRF52-10K
R3: R22.1; R_Axial_DIN0207_L6.3mm_D2.5mm_P10.16mm_Horizontal; MFG # RNF14FTD22R1
R6: R44.2; R_Axial_DIN0207_L6.3mm_D2.5mm_P10.16mm_Horizontal; MFG # MFR-25FRF52-44R2
R11: R88.7; R_Axial_DIN0207_L6.3mm_D2.5mm_P10.16mm_Horizontal; MFG # MFR-25FBF52-88R7
R12: R178; R_Axial_DIN0207_L6.3mm_D2.5mm_P10.16mm_Horizontal; MFG # MFR-25FBF52-178R
R16: R357; R_Axial_DIN0207_L6.3mm_D2.5mm_P10.16mm_Horizontal; MFG # MFR-25FBF52-357R
R20: R715; R_Axial_DIN0207_L6.3mm_D2.5mm_P10.16mm_Horizontal; MFG # MFR-25FBF52-715R
R21: R1.43k; R_Axial_DIN0207_L6.3mm_D2.5mm_P10.16mm_Horizontal; MFG # MFR-25FBF52-1K43
R36: R2.87k; R_Axial_DIN0207_L6.3mm_D2.5mm_P10.16mm_Horizontal; MFG # MFR-25FBF52-2K87
R37: R5.76k; R_Axial_DIN0207_L6.3mm_D2.5mm_P10.16mm_Horizontal; MFG # MFR-25FRF52-5K76
R38: R11.5k; R_Axial_DIN0207_L6.3mm_D2.5mm_P10.16mm_Horizontal; MFG # MFR-25FBF52-11K5
R39: R23.2k; R_Axial_DIN0207_L6.3mm_D2.5mm_P10.16mm_Horizontal; MFG # MFR-25FBF52-11K5
R40: R46.4k; R_Axial_DIN0207_L6.3mm_D2.5mm_P10.16mm_Horizontal; MFG # MFR-25FRF52-46K4
R41: R93.1k; R_Axial_DIN0207_L6.3mm_D2.5mm_P10.16mm_Horizontal; MFG # MFR-25FBF52-93K1
U1: STM32C092KCT6; LQFP-32_7x7mm_P0.8mm; Part # STM32C092KCT6
U2: LP2985-3.3; SOT-23-5
U3, U4, U5, U6, U7, U8, U9, U10, U11, U12, U13, U14, U15, U16, U17: LH1546AT; DIP762W50P254L730H410Q6

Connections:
+3.3V: C1.1, C2.1, C5.1, D4.2 (A2), J1.1 (VCC), J5.1, J10.1, U1.4 (VDD/VDDA), U2.5 (VOUT)
+5V: C6.1, D3.1 (A1), J2.1, R1.1, R5.1, R9.1, R10.1, R17.1, R18.1, R19.1, R29.1, R30.1, R31.1, R32.1, R33.1, R34.1, R35.2, R42.2, U2.1 (VIN), U2.3 (ON/~OFF)
/Bit0: R7.2, U1.23 (PA12[PA10])
/Bit1: R8.2, U1.26 (PA15)
/Bit2: R13.2, U1.27 (PB3)
/Bit3: R14.2, U1.28 (PB4)
/Bit4: R15.2, U1.29 (PB5)
/Bit5: R22.2, U1.30 (PB6)
/Bit6: R23.2, U1.31 (PB7)
/Bit7: R24.2, U1.32 (PB8)
/Bit8: R25.2, U1.9 (PA2)
/Bit9: R26.2, U1.10 (PA3)
/Bit10: R27.2, U1.11 (PA4)
/Bit11: R28.2, U1.12 (PA5)
/Bit12: R43.2, U1.13 (PA6)
/FootPedalPotOutput: D2.1 (A/K_1), J3.1, U1.8 (PA1)
/Line-NC1: U3.5
/Line-NC2: U4.5
/Line-NC3: U5.5
/Line-NC4: U6.5
/Line-NC5: U7.5
/Line-NC6: U8.5
/Line-NC7: U9.5
/Line-NC8: U15.5
/Line-NC9: U14.5
/Line-NC10: U12.5
/Line-NC11: U11.5
/Line-NC12: U10.5
/Line-NC13: U17.5
/Line-NC14: U16.5
/Line-NC15: U13.5
/Line-R1: R3.1, U3.6, U17.4
/Line-R2: R3.2, R6.1, U3.4, U4.6
/Line-R3: R6.2, R11.1, U4.4, U5.6
/Line-R4: R11.2, R12.1, U5.4, U6.6
/Line-R5: R12.2, R16.1, U6.4, U7.6
/Line-R6: R16.2, R20.1, U7.4, U8.6
/Line-R7: R20.2, R21.1, U8.4, U9.6
/Line-R8: R21.2, R36.2, U9.4, U15.4
/Line-R9: R36.1, R37.2, U14.4, U15.6
/Line-R10: R37.1, R38.2, U13.4, U14.6
/Line-R11: R38.1, R39.2, U12.4, U13.6
/Line-R12: R39.1, R40.2, U11.4, U12.6
/Line-R13: R40.1, R41.2, U10.4, U11.6
/Line-R-In: J6.1, R41.1, U10.6, U16.6
/Line-R-Out: J7.1, U16.4, U17.6
/MaxResBit: R4.1, U1.22 (PA11[PA9])
/MinResBit: R2.1, U1.21 (PA10)
/rotary-encoder-output: D2.2 (A/K_2), J9.1, U1.18 (PA8)
GND: C1.2, C2.2, C3.2, C4.2, C5.2, C6.2, D1.3 (COM_A), D2.3 (COM_A), D3.2 (A2), D4.1 (A1), J1.5 (GND), J2.2, J4.1, J8.1, Q1.1 (E), Q2.1 (E), Q3.1 (E), Q4.1 (E), Q5.1 (E), Q6.1 (E), Q7.1 (E), Q8.1 (E), Q9.1 (E), Q10.1 (E), Q11.1 (E), Q12.1 (E), Q13.1 (E), Q14.1 (E), Q15.1 (E), U1.5 (VSS/VSSA), U2.2 (GND)
unnamed: D1.1 (A/K_1), J1.4 (SWCLK), U1.25 (PA14-BOOT0)
unnamed: D1.2 (A/K_2), J1.2 (SWDIO), U1.24 (PA13)
unnamed: C3.1, J1.3 (~RESET), U1.6 (PF2-NRST)
unnamed: Q1.2 (B), R7.1
unnamed: Q1.3 (C), U3.2
unnamed: Q2.2 (B), R8.1
unnamed: Q2.3 (C), U4.2
unnamed: Q3.2 (B), R13.1
unnamed: Q3.3 (C), U5.2
unnamed: Q4.2 (B), R14.1
unnamed: Q4.3 (C), U6.2
unnamed: Q5.2 (B), R15.1
unnamed: Q5.3 (C), U7.2
unnamed: Q6.2 (B), R22.1
unnamed: Q6.3 (C), U8.2
unnamed: Q7.2 (B), R23.1
unnamed: Q7.3 (C), U9.2
unnamed: Q8.2 (B), R43.1
unnamed: Q8.3 (C), U10.2
unnamed: Q9.2 (B), R28.1
unnamed: Q9.3 (C), U11.2
unnamed: Q10.2 (B), R27.1
unnamed: Q10.3 (C), U12.2
unnamed: Q11.2 (B), R26.1
unnamed: Q11.3 (C), U13.2
unnamed: Q12.2 (B), R25.1
unnamed: Q12.3 (C), U14.2
unnamed: Q13.2 (B), R24.1
unnamed: Q13.3 (C), U15.2
unnamed: Q14.2 (B), R2.2
unnamed: Q14.3 (C), U16.2
unnamed: Q15.2 (B), R4.2
unnamed: Q15.3 (C), U17.2
unnamed: R1.2, U3.1
unnamed: R5.2, U4.1
unnamed: R9.2, U5.1
unnamed: R10.2, U6.1
unnamed: R17.2, U7.1
unnamed: R18.2, U8.1
unnamed: R19.2, U9.1
unnamed: R29.2, U10.1
unnamed: R30.2, U11.1
unnamed: R31.2, U12.1
unnamed: R32.2, U13.1
unnamed: R33.2, U14.1
unnamed: R34.2, U15.1
unnamed: R35.1, U16.1
unnamed: R42.1, U17.1
unnamed: C4.1, U2.4 (BP)

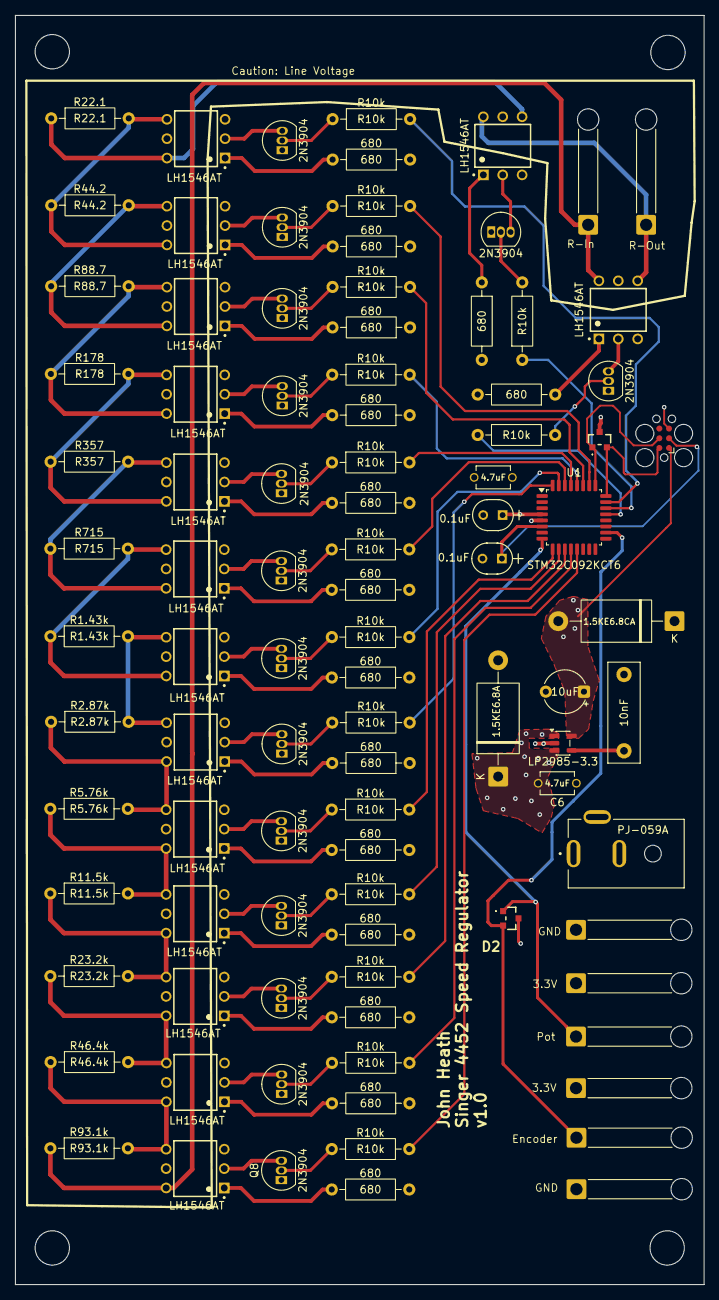
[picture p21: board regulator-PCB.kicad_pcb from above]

Board: 4 copper layers, 90.3 x 166.4 mm, 99 parts (0 on the bottom side), 84 nets.

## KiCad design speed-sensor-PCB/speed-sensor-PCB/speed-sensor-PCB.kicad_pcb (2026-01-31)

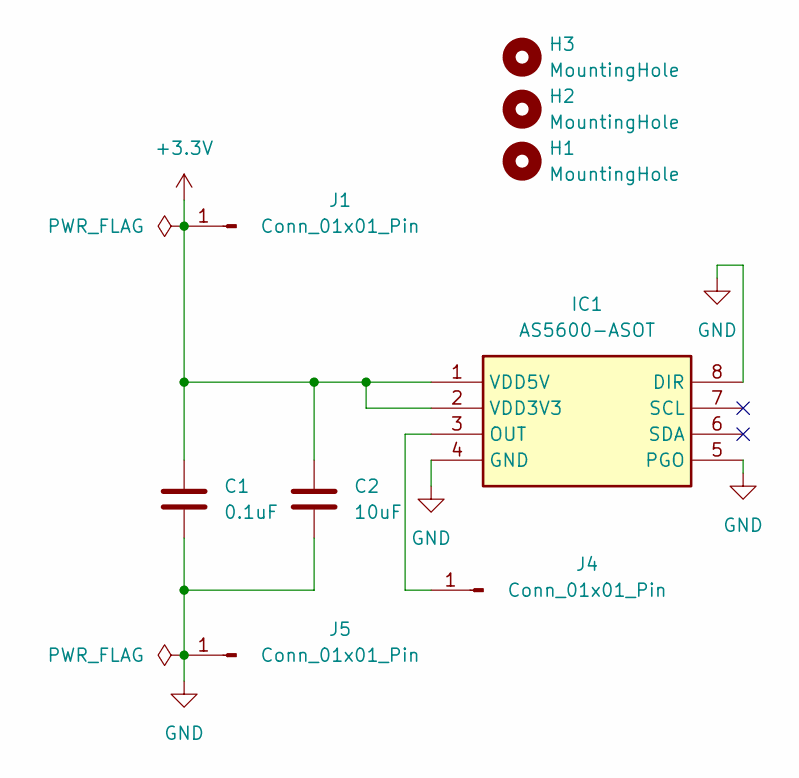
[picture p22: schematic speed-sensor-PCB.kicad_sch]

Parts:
C1: 0.1uF; C_Disc_D5.0mm_W2.5mm_P2.50mm; Part # C320C104K5R5TA
C2: 10uF; CP_Radial_Tantal_D5.5mm_P5.00mm; Part # FG20X7R1H106KRT06
H1, H2, H3: MountingHole; MountingHole_6.4mm_M6_ISO14580
IC1: AS5600-ASOT; SOIC-8_3.9x4.9mm_P1.27mm; Mouser Part Number 985-AS5600-ASOT
J1, J4, J5: Conn_01x01_Pin; SolderWire-0.5sqmm_1x01_D0.9mm_OD2.1mm_Relief

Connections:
+3.3V: C1.1, C2.1, IC1.1 (VDD5V), IC1.2 (VDD3V3), J1.1
GND: C1.2, C2.2, IC1.4 (GND), IC1.5 (PGO), IC1.8 (DIR), J5.1
unnamed: IC1.3 (OUT), J4.1

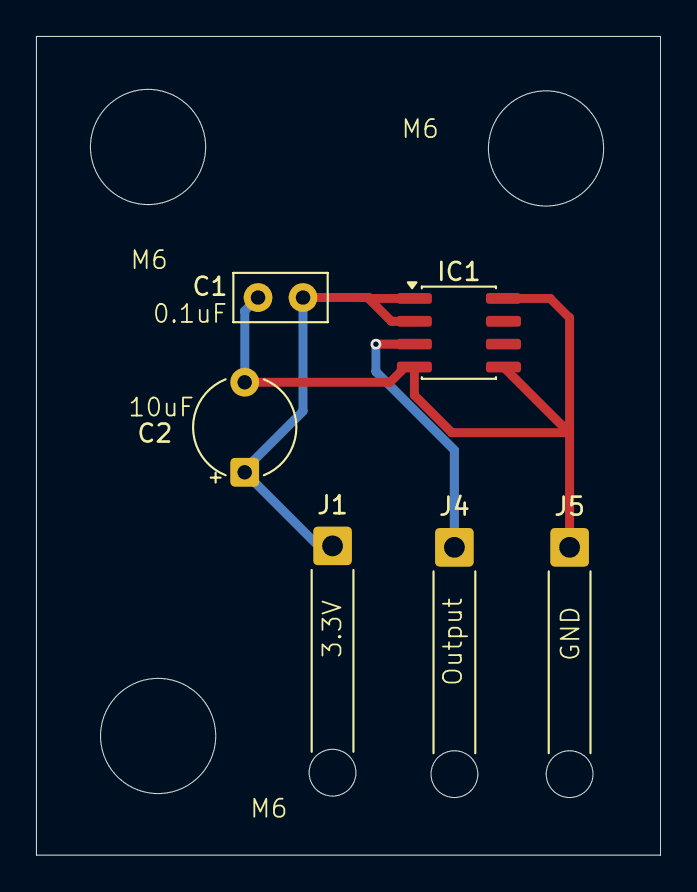
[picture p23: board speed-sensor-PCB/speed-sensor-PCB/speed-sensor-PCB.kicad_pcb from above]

Board: 2 copper layers, 34.7 x 45.5 mm, 9 parts (0 on the bottom side), 3 nets.

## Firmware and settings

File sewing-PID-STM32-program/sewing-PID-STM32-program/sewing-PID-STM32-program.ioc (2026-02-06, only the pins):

Mcu.UserName=STM32C092KCTx
PA1.Signal=ADC1_IN1
PA10.Signal=GPIO_Output
PA15.Signal=GPIO_Output
PA2.Signal=GPIO_Output
PA3.Signal=GPIO_Output
PA4.Signal=GPIO_Output
PA5.Signal=GPIO_Output
PA6.Signal=GPIO_Output
PA8.Signal=ADC1_IN8
PB3.Signal=GPIO_Output
PB4.Signal=GPIO_Output
PB5.Signal=GPIO_Output
PB6.Signal=GPIO_Output
PB7.Signal=GPIO_Output
PB8.Signal=GPIO_Output

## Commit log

2026-01-26 gitignore edits for kicad
2026-01-26 added chamfer to stabilizer
    [260124-Grip.FCStd, 260125-lower-PCB-mount.stl, 260125-upper-PCB-mount.stl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]
2026-01-27 initial schematic for regulator PCB
    [260127-order.xlsx, regulator-PCB.kicad_pcb, regulator-PCB.kicad_sch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]
2026-01-29 ordered JST VH and made speed sensor PCB design
    [260128-order.xlsx, regulator-PCB.kicad_sch, speed-controller-parts-brainstorm.xlsx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]
2026-01-29 Regular PCB schematic completed. Drafted a poor design for the regulator PCB, then added line voltage safety constraints. Pending PCB redesign.
    [regulator-PCB.kicad_pcb, regulator-PCB.kicad_sch, speed-controller-parts-brainstorm.xlsx]
2026-01-29 Regulator PCB v1.0 designed and ordered.
    [regulator-PCB-B_Cu.gbr, regulator-PCB-B_Mask.gbr, regulator-PCB-B_Paste.gbr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]
2026-01-29 cleaning up ordering
    [260120-McMaster.xlsx, speed-controller-parts-brainstorm.xlsx]
2026-01-31 worked out schematic for foot pedal PCB via reverse engineering and LTSpice
    [foot-pedal-PCB.kicad_pcb, foot-pedal-PCB.kicad_sch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]
2026-02-01 fleshed out SPICE, finished pedal schematic v1.0, ordered pedal BOM from mouser.
    [BOM.csv, foot-pedal-PCB.kicad_pcb, foot-pedal-PCB.kicad_sch]
2026-02-02 Added circuit protection, finished foot pedal PCB design, ordered from OSHPark
    [board_outline.FCStd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]
2026-02-06 working on program, fixed PGO connection on speed detector PCB
    [260127-order-digikey.xlsx, BOM.csv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]
2026-02-06 implementing PID
2026-02-12 README update
    [260120-McMaster.xlsx, speed-controller-parts-brainstorm.xlsx]
2026-02-16 increased pot threshold to prevent motor bursts without pedal input
